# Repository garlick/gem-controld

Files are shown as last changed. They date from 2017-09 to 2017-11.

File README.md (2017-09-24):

### gem-controld

This project is a control system for a german equatorial telescope mount.
The mount is a Parallax series 125 head that has been retrofitted
with stepper motors on RA and DEC axes.

Electronics are based on the Beaglebone Black ARM-based single board
computer running Linux, a custom interface "cape" with two
[RS-422 transceivers](http://www.ti.com/product/sn65hvd379) which connect to
[Schneider Electric IM483i](http://motion.schneider-electric.com/downloads/manuals/im483i_ie.pdf) motion controllers, and GPIO based
[autogider](http://www.store.shoestringastronomy.com/guide_port_cables.pdf) and
[handbox](http://www.bbastrodesigns.com/handpad-assembly_notes.html) interfaces.
The electronics are packaged in a 7x7x5 DIN rail enclosure that mounts to
the telescope pier.

Software is based on reactive (event-driven) programming, with the goal
of keeping complexity down and separation of concerns among modules up.

### status

The handbox can be used to slew the telescope in two speeds, and the RA axis
tracks at a fixed sidereal rate.

The Meade LX200 and Tangent BBOX protocols can be used to sync the telescope
with a starmap program like Sky Safari, or control it (LX200 only).  A simple
pointing model is implemented with a one-star alignment available through
the remote application.

Autoguiding on an ST-4 interface works.

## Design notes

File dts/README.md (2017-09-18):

### device tree overlay

`GEM-IO` is the device tree overlay for the "cape" used in this project.
This description assumes Debian Jessie with kernel 4.x or similar.

We need the device tree compiler `dtc`:
```
sudo apt-get install device-tree-compiler
```

After installing compiled dtbo file into `/lib/firmware`, add
it to `/etc/default/capemgr`.
```
CAPE=GEM-IO
```

By default GEM-IO conflicts with  `BB-BONELT-HDMI`.  Disable it by following
instructions in `/boot/uEnv.txt`.  Currently it is to uncomment this
line:
```
##BeagleBone Black: HDMI (Audio/Video)/eMMC disabled:
#dtb=am335x-boneblack-overlay.dtb
```

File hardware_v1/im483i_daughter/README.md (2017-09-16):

### IM483i daughter board for GEM

This is a daughter board for the Intelligent Motion Systems, Inc
IM483i minature high performance microstepping module.  It breaks
out the RS-422 and hand controller inputs, and ties some outputs to
LED's mounted on the board.

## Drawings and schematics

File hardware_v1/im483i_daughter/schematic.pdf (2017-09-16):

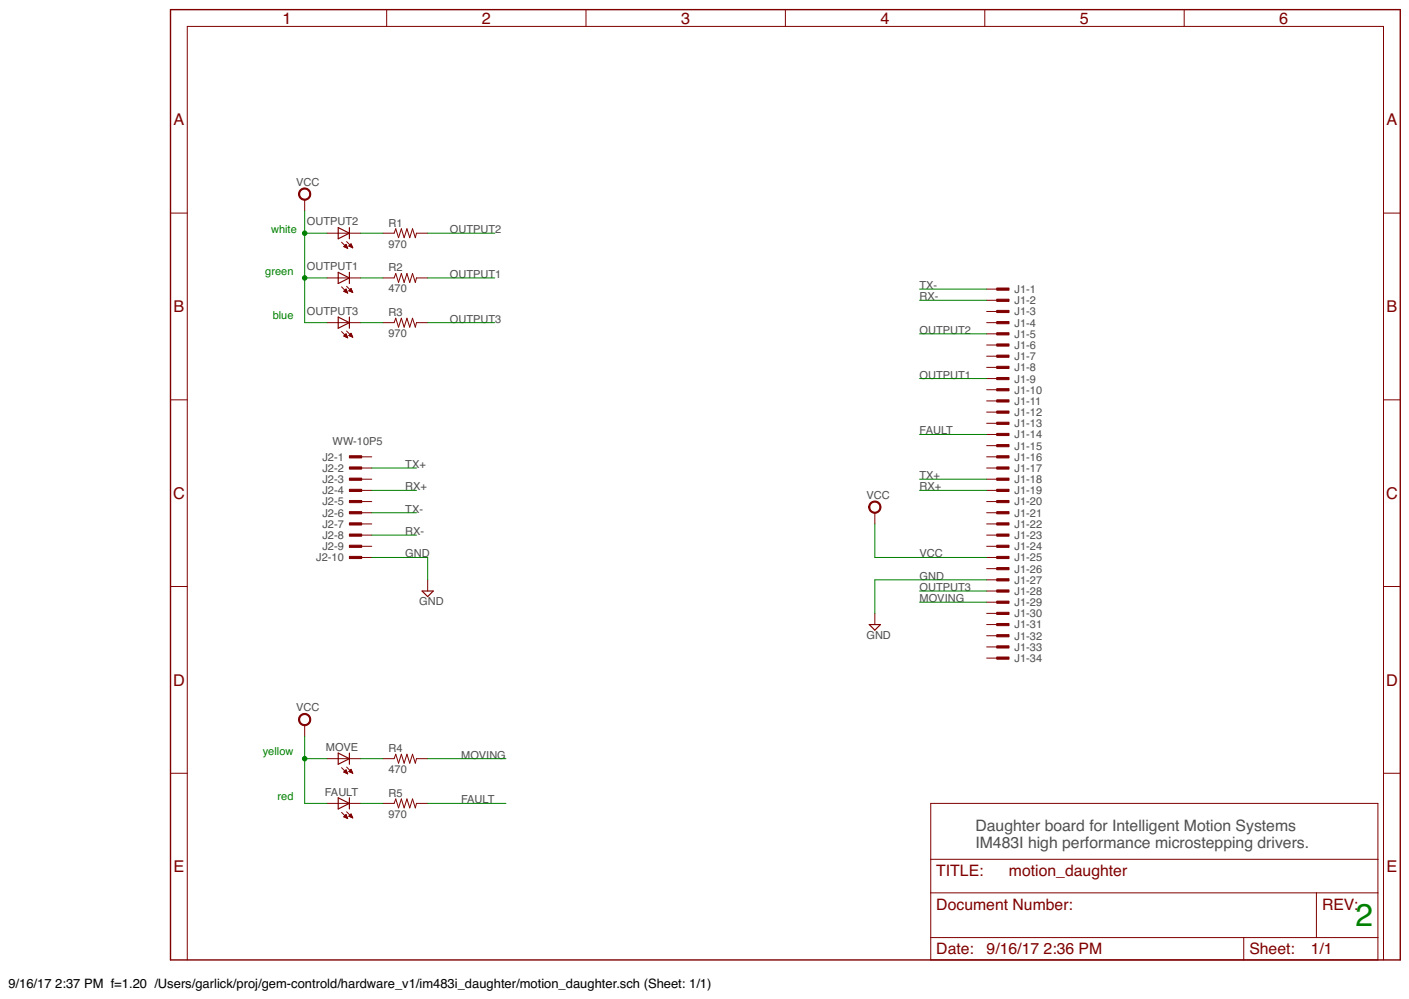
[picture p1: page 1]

Daughter board for Intelligent Motion Systems
IM483I high performance microstepping drivers.
TITLE:

Document Number: | REV: 2

Date: 9/16/17 2:36 PM | Sheet: 1/1

9/16/17 2:37 PM f=1.20 /Users/garlick/proj/gem-controld/hardware_v1/im483i_daughter/motion_daughter.sch (Sheet: 1/1)

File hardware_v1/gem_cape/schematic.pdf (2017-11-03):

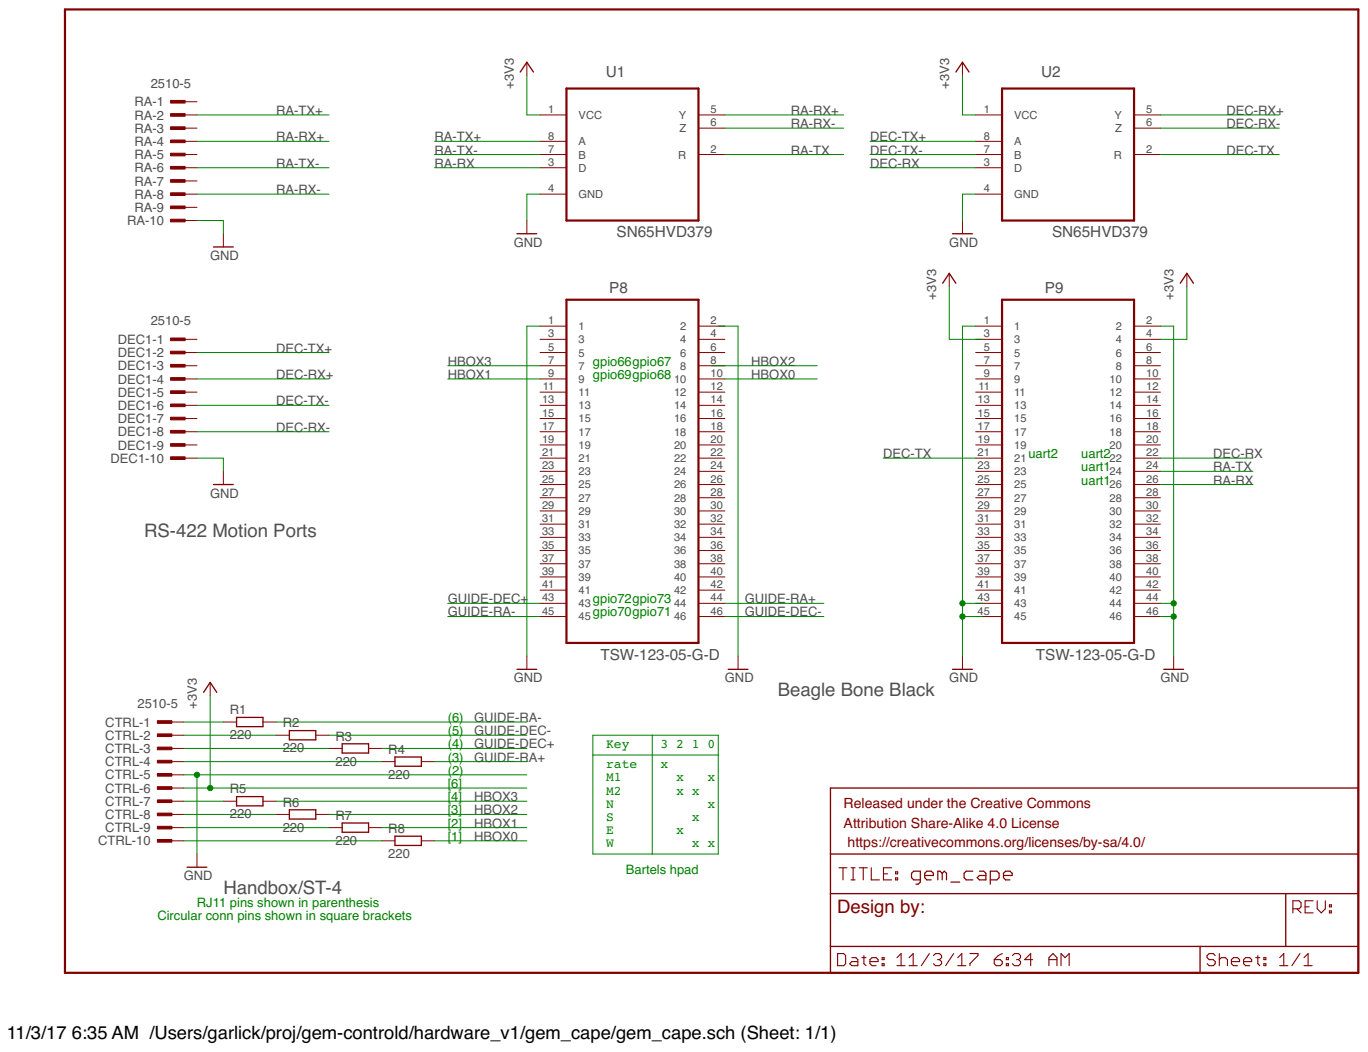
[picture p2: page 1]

DEC-RX- RA-TX

5 7 9 11 13 15 17 19 21 | 6 8 10 12 14 16 18 20 22

GUIDE-DEC+
GUIDE-RA-

GUIDE-DEC-

Key | 3 2 1 0
rate M1 M2 N S E | x x x x

Released under the Creative Commons Attribution Share-Alike 4.0 License

https://creativecommons.org/licenses/by-sa/4.0/

RJ11 pins shown in parenthesis Circular conn pins shown in square brackets

11/3/17 6:35 AM /Users/garlick/proj/gem-controld/hardware_v1/gem_cape/gem_cape.sch (Sheet: 1/1)

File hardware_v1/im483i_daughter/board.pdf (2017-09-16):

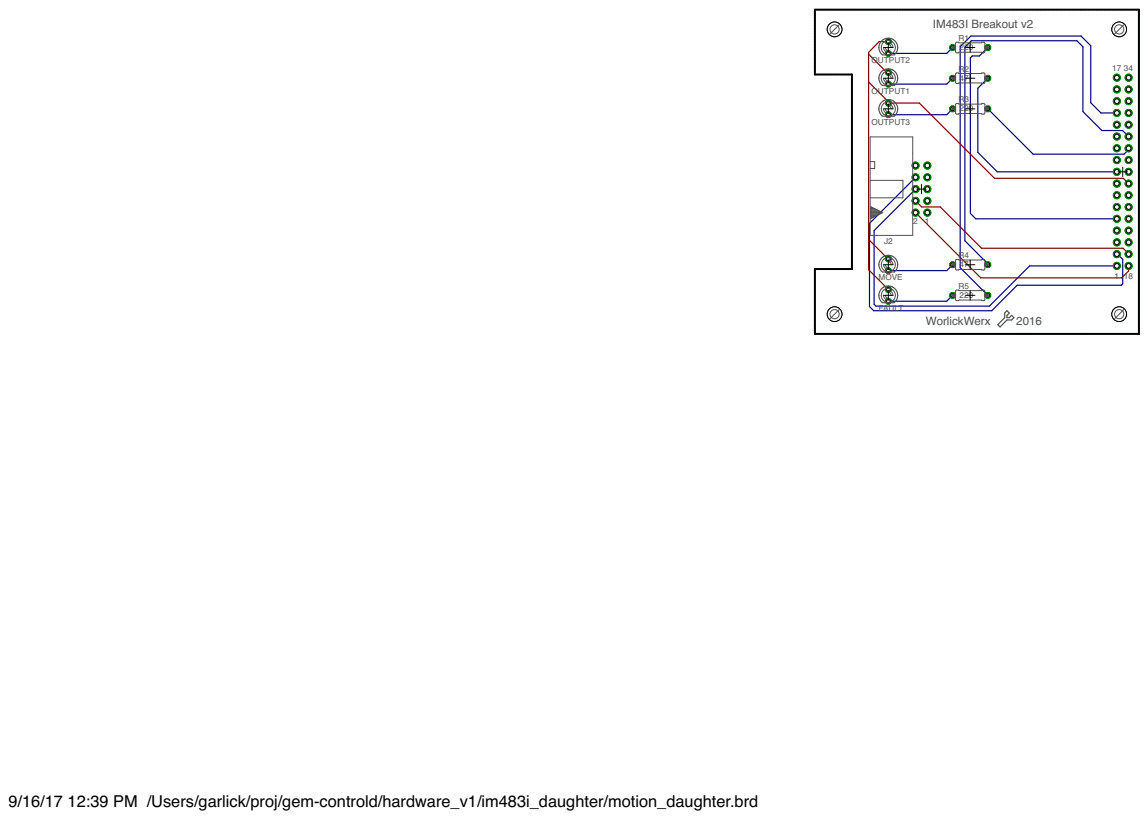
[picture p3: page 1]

9/16/17 12:39 PM /Users/garlick/proj/gem-controld/hardware_v1/im483i_daughter/motion_daughter.brd

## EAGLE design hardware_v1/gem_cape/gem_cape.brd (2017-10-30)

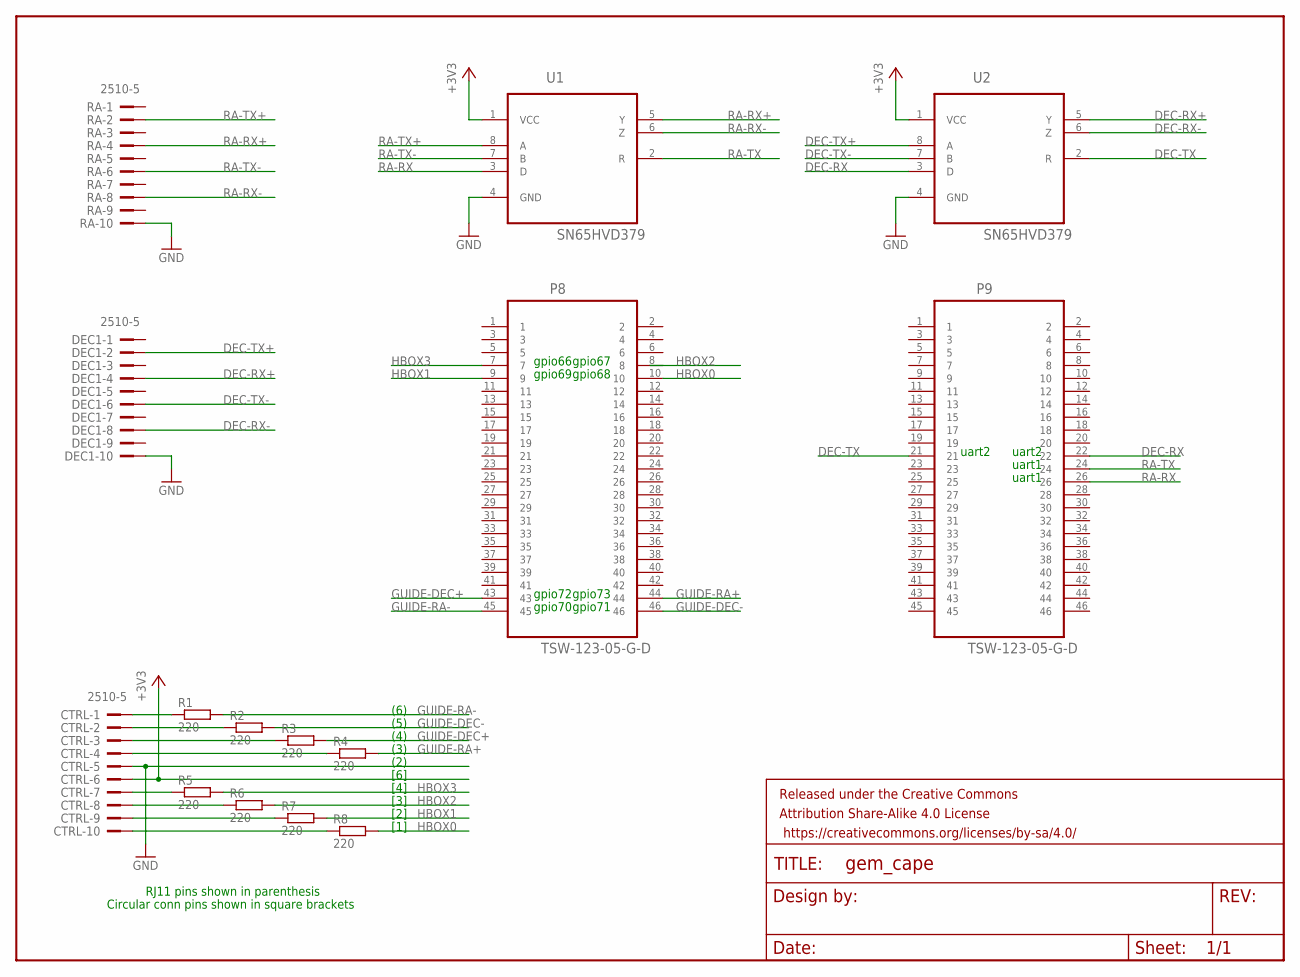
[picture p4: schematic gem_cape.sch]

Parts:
CTRL: 2510-5; PAK100/2500-5-10
DEC1: 2510-5; PAK100/2500-5-10
FRAME1: FRAME-LETTER; CREATIVE_COMMONS
P8, P9: TSW-123-05-G-D; SAMTEC_TSW-123-05-G-D
R1, R2, R3, R4, R5, R6, R7, R8: 220; R0805
RA: 2510-5; PAK100/2500-5-10
U1, U2: SN65HVD379; SOIC127P600X175-8N; MPN SN65HVD379

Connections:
+3V3: CTRL.6, U1.1 (VCC), U2.1 (VCC)
DEC-RX: P9.22, U2.3 (D)
DEC-RX+: DEC1.4, U2.5 (Y)
DEC-RX-: DEC1.8, U2.6 (Z)
DEC-TX: P9.21, U2.2 (R)
DEC-TX+: DEC1.2, U2.8 (A)
DEC-TX-: DEC1.6, U2.7 (B)
GND: CTRL.5, DEC1.10, RA.10, U1.4 (GND), U2.4 (GND)
GUIDE-DEC+: P8.43, R3.2
GUIDE-DEC-: P8.46, R2.2
GUIDE-RA+: P8.44, R4.2
GUIDE-RA-: P8.45, R1.2
HBOX0: P8.10, R8.2
HBOX1: P8.9, R7.2
HBOX2: P8.8, R6.2
HBOX3: P8.7, R5.2
unnamed: CTRL.1, R1.1
unnamed: CTRL.2, R2.1
unnamed: CTRL.3, R3.1
unnamed: CTRL.4, R4.1
unnamed: CTRL.7, R5.1
unnamed: CTRL.8, R6.1
unnamed: CTRL.9, R7.1
unnamed: CTRL.10, R8.1
RA-RX: P9.26, U1.3 (D)
RA-RX+: RA.4, U1.5 (Y)
RA-RX-: RA.8, U1.6 (Z)
RA-TX: P9.24, U1.2 (R)
RA-TX+: RA.2, U1.8 (A)
RA-TX-: RA.6, U1.7 (B)

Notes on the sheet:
(6)
(5)
(4)
(3)
(2)
[6]
[4]
[3]
[2]
[1]
RJ11 pins shown in parenthesis
Circular conn pins shown in square brackets
uart2
uart1
gpio68
gpio69
gpio67
gpio66
gpio72
gpio71
gpio73
gpio70

Board: 2 copper layers, 16 parts (2 on the bottom side), 30 nets, no tracks yet.

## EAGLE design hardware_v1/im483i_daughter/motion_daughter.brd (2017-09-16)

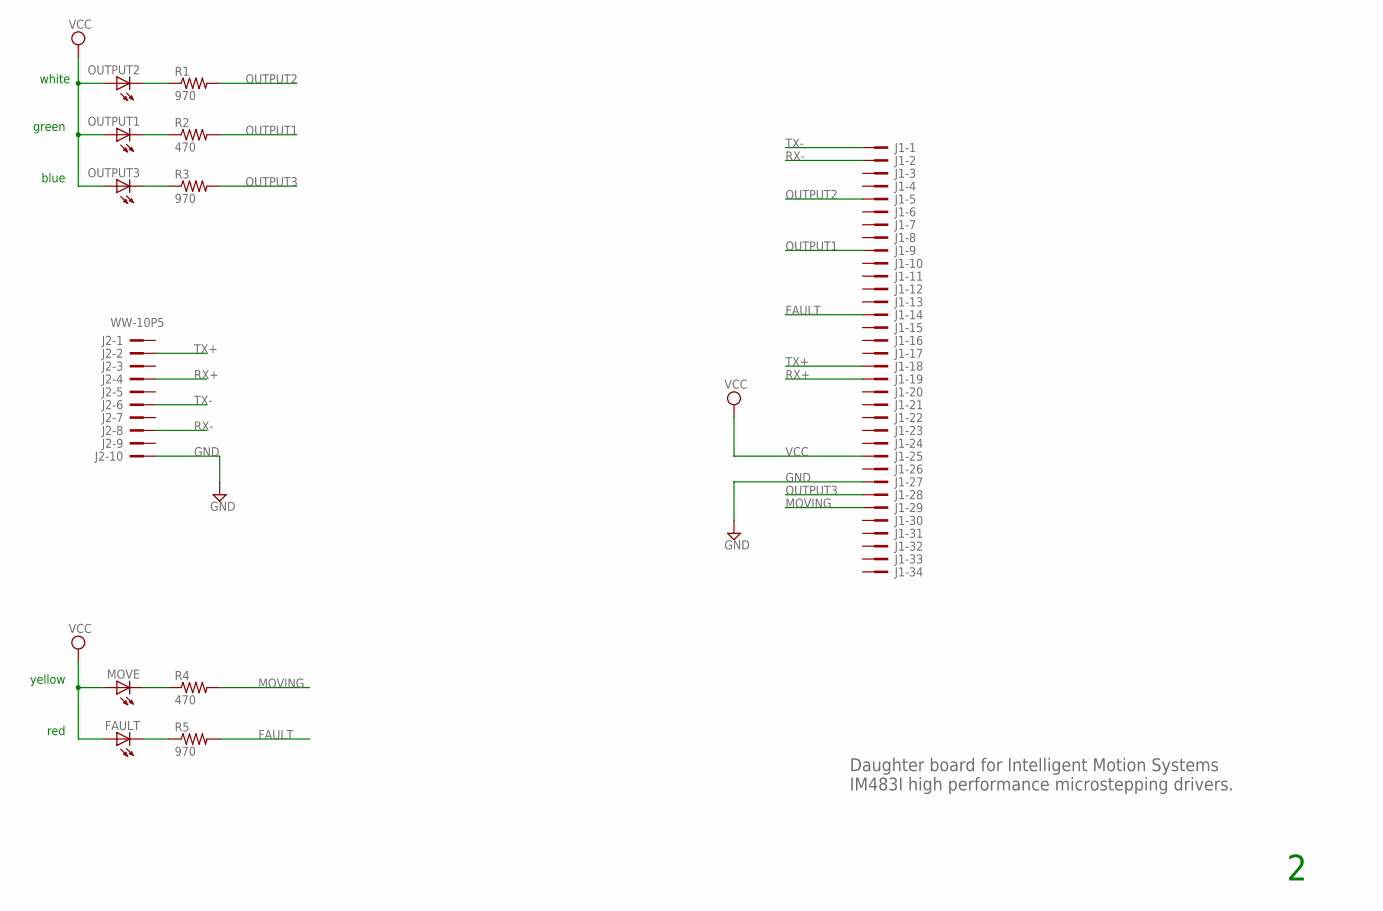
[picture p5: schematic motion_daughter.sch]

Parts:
FAULT: LED3MM
J1: WW-34P-SPECIALIM483I_HEADER; PAK100/2500-34
J2: WW-10P5; PAK100/2500-5-10
MOVE: LED3MM
OUTPUT1, OUTPUT2, OUTPUT3: LED3MM
R1, R3, R5: 970; 0207/7
R2, R4: 470; 0207/7

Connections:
FAULT: J1.P14, R5.2
GND: J1.P27, J2.10
MOVING: J1.P29, R4.2
unnamed: OUTPUT3.K (C), R3.1
unnamed: OUTPUT1.K (C), R2.1
unnamed: OUTPUT2.K (C), R1.1
unnamed: MOVE.K (C), R4.1
unnamed: FAULT.K (C), R5.1
OUTPUT1: J1.P9, R2.2
OUTPUT2: J1.P5, R1.2
OUTPUT3: J1.P28, R3.2
RX+: J1.P19, J2.4
RX-: J1.P2, J2.8
TX+: J1.P18, J2.2
TX-: J1.P1, J2.6
VCC: FAULT.A, J1.P25, MOVE.A, OUTPUT1.A, OUTPUT2.A, OUTPUT3.A

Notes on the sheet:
Daughter board for Intelligent Motion Systems IM483I high performance microstepping drivers.
white
green
blue
yellow
red

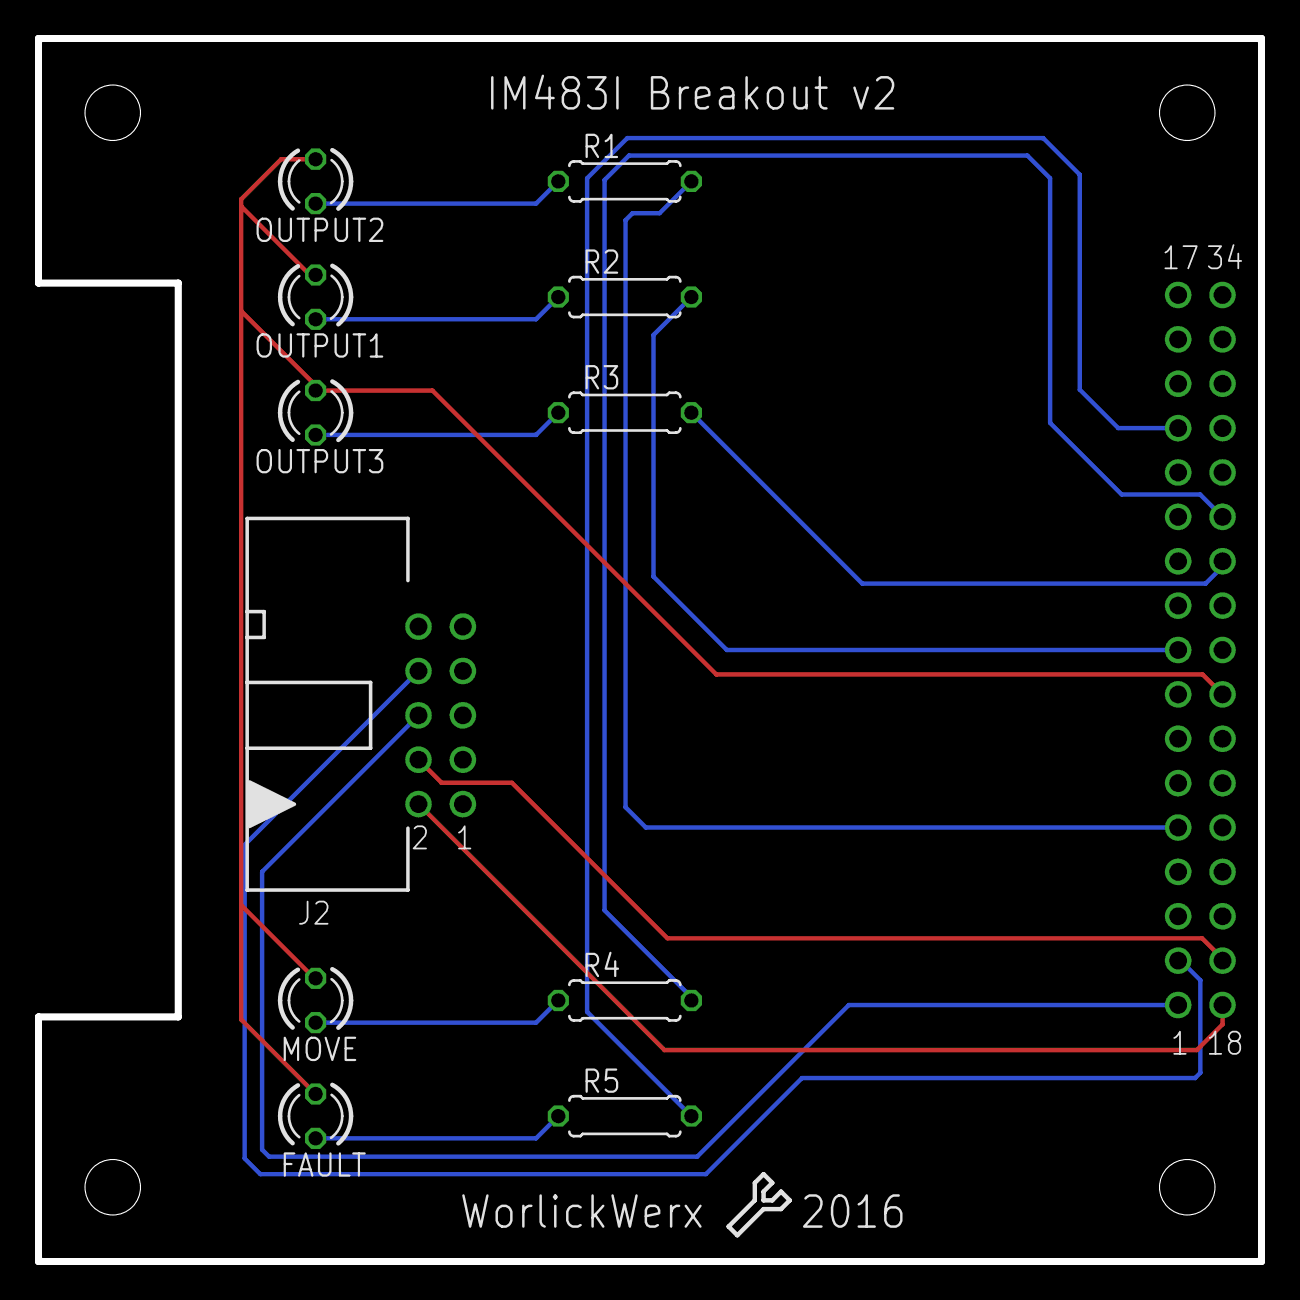
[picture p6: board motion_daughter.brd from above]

Board: 2 copper layers, 70.0 x 70.0 mm, 12 parts (0 on the bottom side), 16 nets.

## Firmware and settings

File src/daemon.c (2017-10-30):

/*****************************************************************************\
 *  Copyright (C) 2015 Jim Garlick
 *  Written by Jim Garlick <garlick.jim@gmail.com>
 *  All Rights Reserved.
 *
 *  This file is part of gem-controld
 *  For details, see <https://github.com/garlick/gem-controld>
 *
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
 *  You should have received a copy of the GNU General Public License along
 *  with this program; if not, write to the Free Software Foundation, Inc.,
 *  59 Temple Place, Suite 330, Boston, MA 02111-1307 USA.
 *  See also:  http://www.gnu.org/licenses/
\*****************************************************************************/

#include <stdio.h>
#include <stdlib.h>
#include <stdbool.h>
#include <unistd.h>
#include <libgen.h>
#include <getopt.h>
#include <errno.h>
#include <string.h>
#include <pwd.h>
#include <ev.h>
#include <math.h>
#include <assert.h>

#include "log.h"
#include "xzmalloc.h"
#include "gpio.h"
#include "configfile.h"
#include "motion.h"
#include "slew.h"
#include "hpad.h"
#include "guide.h"
#include "bbox.h"
#include "lx200.h"

char *prog = "";

struct prog_context {
    struct config opt;
    struct hpad *hpad;
    struct guide *guide;
    struct bbox *bbox;
    struct lx200 *lx200;
    struct motion *t;
    struct motion *d;
    struct ev_loop *loop;
    bool t_tracking;
    int slew;
    bool west;
};

struct motion *init_axis (struct config_axis *a, const char *name, int flags,
                          bool ccw);

void hpad_cb (struct hpad *h, void *arg);
void guide_cb (struct guide *g, void *arg);
void bbox_cb (struct bbox *bb, void *arg);
void motion_cb (struct motion *m, void *arg);
void lx200_pos_ha_cb (struct lx200 *lx, void *arg);
void lx200_pos_dec_cb (struct lx200 *lx, void *arg);
void lx200_slew_cb (struct lx200 *lx, void *arg);
void lx200_goto_cb (struct lx200 *lx, void *arg);
void lx200_stop_cb (struct lx200 *lx, void *arg);
void lx200_tracking_cb (struct lx200 *lx, void *arg);

int controller_velocity (struct config_axis *axis, double degrees_persec);

#define OPTIONS "+c:hMBLHGw"
static const struct option longopts[] = {
    {"config",               required_argument, 0, 'c'},
    {"help",                 no_argument,       0, 'h'},
    {"debug-motion",         no_argument,       0, 'M'},
    {"debug-bbox",           no_argument,       0, 'B'},
    {"debug-lx200",          no_argument,       0, 'L'},
    {"debug-hpad",           no_argument,       0, 'H'},
    {"debug-guide",          no_argument,       0, 'G'},
    {"west",                 no_argument,       0, 'w'},
    {0, 0, 0, 0},
};

static void usage (void)
{
    fprintf (stderr,
"Usage: gem [OPTIONS]\n"
"    -c,--config FILE    set path to config file\n"
"    -w,--west           observe west of meridian (scope east of pier)\n"
"    -M,--debug-motion   emit motion control commands and responses to stderr\n"
"    -B,--debug-bbox     emit bbox protocol to stderr\n"
"    -L,--debug-lx200    emit lx200 protocol to stderr\n"
"    -H,--debug-hpad     emit hpad events to stderr\n"
"    -G,--debug-guide    emit guide pulse events to stderr\n"
);
    exit (1);
}

int main (int argc, char *argv[])
{
    int ch;
    struct prog_context ctx;
    char *config_filename = NULL;
    int motion_flags = 0;
    int bbox_flags = 0;
    int hpad_flags = 0;
    int guide_flags = 0;
    int lx200_flags = 0;

    memset (&ctx, 0, sizeof (ctx));

    prog = basename (argv[0]);
    log_init (prog);

    while ((ch = getopt_long (argc, argv, OPTIONS, longopts, NULL)) != -1) {
        switch (ch) {
            case 'c':   /* --config FILE */
                config_filename = xstrdup (optarg);
                break;
            case 'M':   /* --debug-motion */
                motion_flags |= MOTION_DEBUG;
                break;
            case 'B':   /* --debug-bbox */
                bbox_flags |= BBOX_DEBUG;
                break;
            case 'L':   /* --debug-lx200 */
                lx200_flags |= LX200_DEBUG;
                break;
            case 'H':   /* --debug-hpad */
                hpad_flags |= HPAD_DEBUG;
                break;
            case 'G':   /* --debug-guide */
                guide_flags |= GUIDE_DEBUG;
                break;
            case 'w':   /* --west */
                ctx.west = true;
                lx200_flags |= LX200_POINT_WEST; // hint for unaligned starting
                break;
            case 'h':   /* --help */
            default:
                usage ();
        }
    }
    if (optind < argc)
        usage ();
    configfile_init (config_filename, &ctx.opt);
    if (!ctx.opt.hpad_gpio)
        msg_exit ("no hpad_gpio was configured");
    if (!ctx.opt.guide_gpio)
        msg_exit ("no guide_gpio was configured");

    if (!(ctx.loop = ev_loop_new (EVFLAG_AUTO)))
        err_exit ("ev_loop_new");

    ctx.t = init_axis (&ctx.opt.t, "t", motion_flags, true);
    motion_set_cb (ctx.t, motion_cb, &ctx);
    motion_start (ctx.loop, ctx.t);

    ctx.d = init_axis (&ctx.opt.d, "d", motion_flags, ctx.west ? true : false);
    motion_set_cb (ctx.d, motion_cb, &ctx);
    motion_start (ctx.loop, ctx.d);

    ctx.hpad = hpad_new ();
    if (hpad_init (ctx.hpad, ctx.opt.hpad_gpio, ctx.opt.hpad_debounce,
                   hpad_cb, &ctx, hpad_flags) < 0)
        err_exit ("hpad_init");
    hpad_start (ctx.loop, ctx.hpad);

    ctx.guide = guide_new ();
    if (guide_init (ctx.guide, ctx.opt.guide_gpio, ctx.opt.guide_debounce,
                   guide_cb, &ctx, guide_flags) < 0)
        err_exit ("guide_init");
    guide_start (ctx.loop, ctx.guide);

    ctx.bbox = bbox_new ();
    if (bbox_init (ctx.bbox, DEFAULT_BBOX_PORT, bbox_cb, &ctx, bbox_flags) < 0)
        err_exit ("bbox_init");
    bbox_set_resolution (ctx.bbox, ctx.opt.t.steps, ctx.opt.d.steps);
    bbox_start (ctx.loop, ctx.bbox);

    ctx.lx200 = lx200_new ();
    if (lx200_init (ctx.lx200, DEFAULT_LX200_PORT, lx200_flags) < 0)
        err_exit ("bbox_init");
    lx200_set_position_ha_cb (ctx.lx200, lx200_pos_ha_cb, &ctx);
    lx200_set_position_dec_cb (ctx.lx200, lx200_pos_dec_cb, &ctx);
    lx200_set_slew_cb (ctx.lx200, lx200_slew_cb, &ctx);
    lx200_set_goto_cb (ctx.lx200, lx200_goto_cb, &ctx);
    lx200_set_stop_cb (ctx.lx200, lx200_stop_cb, &ctx);
    lx200_set_tracking_cb (ctx.lx200, lx200_tracking_cb, &ctx);
    lx200_start (ctx.loop, ctx.lx200);

    ev_run (ctx.loop, 0);
    ev_loop_destroy (ctx.loop);

    bbox_stop (ctx.loop, ctx.bbox);
    bbox_destroy (ctx.bbox);

    lx200_stop (ctx.loop, ctx.lx200);
    lx200_destroy (ctx.lx200);

    guide_stop (ctx.loop, ctx.guide);
    guide_destroy (ctx.guide);

    hpad_stop (ctx.loop, ctx.hpad);
    hpad_destroy (ctx.hpad);

    motion_destroy (ctx.d);
    motion_destroy (ctx.t);

    return 0;
}

struct motion *init_axis (struct config_axis *a, const char *name, int flags,
                          bool ccw)
{
    struct motion_config cfg = {
        .resolution = a->resolution,
        .ihold      = a->ihold,
        .irun       = a->irun,
        .mode       = a->mode,
        .accel      = a->accel,
        .decel      = a->decel,
        .initv      = a->initv,
        .finalv     = a->finalv,
        .steps      = a->steps,
        .ccw        = ccw,
    };
    struct motion *m;

    if (!a->device)
        msg_exit ("%s: no serial device configured", name);
    if (!(m = motion_new (name)))
        err_exit ("%s: motion_create", name);
    if (motion_init (m, a->device, &cfg, flags) < 0)
        err_exit ("%s: motion_init %s", name, a->device);
    if (motion_set_io (m, MOTION_IO_OUTPUT1 | MOTION_IO_OUTPUT2
                                            | MOTION_IO_OUTPUT3) < 0)
        err_exit ("%s: motion set port", name);
    return m;
}

/* Given 'rate' enum from slew.h, look up configured rate in degrees/sec.
 * If 'neg' is true, make the velocity negative.
 * If 'track' is true, add the sidereal rate.
 */
double lookup_rate (struct config_axis *axis, int rate,
                    bool neg, bool track)
{
    double dps;

    switch (rate) {
        case SLEW_RATE_GUIDE:
            dps = axis->guide;
            break;
        case SLEW_RATE_SLOW:
            dps = axis->slow;
            break;
        case SLEW_RATE_MEDIUM:
            dps = axis->medium;
            break;
        case SLEW_RATE_FAST:
            dps = axis->fast;
            break;
        default:
            dps = 0.;
            break;
    }
    if (neg)
        dps *= -1.;
    if (track)
        dps += axis->sidereal;
    return dps;
}

/* A new slew "key press" event ignores a slew in progress on the
 * same axis and blindly sets the velocity.  The motion controllers can
 * handle this, even if direction is reversed.  The "key release" cancels
 * this and any other slew in progress.  The axes are independent.
 * It is possible to configure slew rates that will result in a controller
 * error;  motion_move_constant_dps() will return -1 with errno == EINVAL in
 * that case and the slew will fail.
 */
void slew_update (struct prog_context *ctx, int newmask, int rate)
{
    double dps;

    if ((newmask & SLEW_RA_PLUS) && (newmask & SLEW_RA_MINUS))
        newmask &= ~(SLEW_RA_PLUS + SLEW_RA_MINUS);
    if ((newmask & SLEW_DEC_PLUS) && (newmask & SLEW_DEC_MINUS))
        newmask &= ~(SLEW_DEC_PLUS + SLEW_DEC_MINUS);

    if ((newmask & SLEW_RA_PLUS) || (newmask & SLEW_RA_MINUS)) {
        dps = lookup_rate (&ctx->opt.t, rate, (newmask & SLEW_RA_MINUS),
                           ctx->t_tracking);
        if (motion_move_constant_dps (ctx->t, dps) < 0)
            err ("t: move at v=%.1lf*/s", dps);
    }
    else {
        if ((ctx->slew & SLEW_RA_PLUS) || (ctx->slew & SLEW_RA_MINUS)) {
            if (ctx->t_tracking) {
                dps = lookup_rate (&ctx->opt.t, 0, false, ctx->t_tracking);
                if (motion_move_constant_dps (ctx->t, dps) < 0)
                    err ("t: move at v=%.1lf*/s", dps);
            }
            else {
                if (motion_soft_stop (ctx->t) < 0) {
                    err ("t: stop");
                    if (motion_abort (ctx->t) < 0)
                        err ("t: abort");
                }
            }
        }
    }
    if ((newmask & SLEW_DEC_PLUS) || (newmask & SLEW_DEC_MINUS)) {
        dps = lookup_rate (&ctx->opt.d, rate, (newmask & SLEW_DEC_MINUS),
                           false);
        if (motion_move_constant_dps (ctx->d, dps) < 0)
            err ("d: move at v=%.1lf*/s", dps);
    }
    else {
        if ((ctx->slew & SLEW_DEC_PLUS) || (ctx->slew & SLEW_DEC_MINUS)) {
            if (motion_soft_stop (ctx->d) < 0) {
                err ("d: stop");
                if (motion_abort (ctx->d) < 0)
                    err ("d: abort");
            }
        }
    }
    ctx->slew = newmask;
}

/* After toggling t_tracking, or completion of a goto,
 * ensure that motion has (re-)enabled or disabled RA tracking
 * as appropraite.
 */
void update_tracking (struct prog_context *ctx)
{
    double dps;

    if (ctx->t_tracking) {
        dps = lookup_rate (&ctx->opt.t, SLEW_RATE_NONE, false, true);
        if (motion_move_constant_dps (ctx->t, dps) < 0)
            err ("t: move at v=%.1lf*/s", dps);
    }
    else {
         if (motion_soft_stop (ctx->t) < 0)
            err ("t: stop");
    }
}

void hpad_cb (struct hpad *h, void *arg)
{
    struct prog_context *ctx = arg;
    int dir = hpad_get_slew_direction (h);
    int rate = hpad_get_slew_rate (h);
    int ctrl = hpad_get_control (h);

    /* M1 - emergency stop
     */
    if ((ctrl & HPAD_CONTROL_M1)) {
        msg ("emergency stop");
        if (motion_abort (ctx->t) < 0) {
            err ("t: motion_abort");
            if (motion_abort (ctx->t) < 0) // one retry
                err ("t: motion_abort");
        }
        if (motion_abort (ctx->d) < 0) {
            err ("d: motion_abort");
            if (motion_abort (ctx->d) < 0) // one retry
                err ("t: motion_abort");
        }
        ctx->t_tracking = false;
        ctx->slew = 0;
        return;
    }
    /* M2 - toggle tracking
     */
    if ((ctrl & HPAD_CONTROL_M2)) {
        ctx->t_tracking = !ctx->t_tracking;
        update_tracking (ctx);
        return;
    }
    /* N,S,E,W
     */
    slew_update (ctx, dir, rate);
}

void guide_cb (struct guide *g, void *arg)
{
    struct prog_context *ctx = arg;
    int dir;

    if ((dir = guide_get_slew_direction (g)) < 0) {
        err ("guide_get_slew_direction");
        return;
    }
    slew_update (ctx, dir, SLEW_RATE_GUIDE);
}

/* LX200 protocol notifies us that slew "button" events
 * have occurred.
 */
void lx200_slew_cb (struct lx200 *lx, void *arg)
{
    struct prog_context *ctx = arg;
    int dir = lx200_get_slew_direction (lx);
    int rate = lx200_get_slew_rate (lx);

    slew_update (ctx, dir, rate);
}

/* Bbox protocol requests that we update "encoder" position.
 */
void bbox_cb (struct bbox *bb, void *arg)
{
    struct prog_context *ctx = arg;
    double t, d;

    if (motion_get_position (ctx->t, &t) < 0) {
        err ("%s: error reading t position", __FUNCTION__);
        return;
    }
    if (motion_get_position (ctx->d, &d) < 0) {
        err ("%s: error reading d position", __FUNCTION__);
        return;
    }
    bbox_set_position (bb, t, d);
}

/* LX200 protocol requests that we update position.
 */
void lx200_pos_ha_cb (struct lx200 *lx, void *arg)
{
    struct prog_context *ctx = arg;
    double t;
    double t_degrees;

    if (motion_get_position (ctx->t, &t) < 0) {
        err ("%s: error reading t position", __FUNCTION__);
        return;
    }
    t_degrees = 360.0 * (t / ctx->opt.t.steps);
    lx200_set_position_ha (lx, t_degrees);
}

void lx200_pos_dec_cb (struct lx200 *lx, void *arg)
{
    struct prog_context *ctx = arg;
    double d;
    double d_degrees;

    if (motion_get_position (ctx->d, &d) < 0) {
        err ("%s: error reading d position", __FUNCTION__);
        return;
    }
    d_degrees = 360.0 * (d / ctx->opt.d.steps);
    lx200_set_position_dec (lx, d_degrees);
}

/* LX200 protocol notifies us that we should retrieve goto target
 * coordinates and slew there.
 */
void lx200_goto_cb (struct lx200 *lx, void *arg)
{
    struct prog_context *ctx = arg;
    double t_degrees, d_degrees;
    double t, d;

    lx200_get_target (lx, &t_degrees, &d_degrees);

    msg ("goto %.1f*, %.1f*", t_degrees, d_degrees);

    if (t_degrees < -120 || t_degrees > 120
                         || d_degrees < -120 || d_degrees > 120) {
        msg ("goto out of range");
        return;
    }

    t = t_degrees/360.0 * ctx->opt.t.steps;
    d = d_degrees/360.0 * ctx->opt.d.steps;

    if (motion_goto_absolute (ctx->t, t) < 0)
        err ("t: set position");
    if (motion_goto_absolute (ctx->d, d) < 0)
        err ("d: set position");
}

/* LX200 protocol wants to stop all motion (abort a goto).
 * Tracking should continue.
 */
void lx200_stop_cb (struct lx200 *lx, void *arg)
{
    struct prog_context *ctx = arg;

    if (motion_soft_stop (ctx->t) < 0) {
        err ("t: soft stop");
        if (motion_abort (ctx->t) < 0)
            err ("t: abort");
    }
    if (motion_soft_stop (ctx->d) < 0) {
        err ("d: soft stop");
        if (motion_abort (ctx->d) < 0)
            err ("t: abort");
    }
    if (ctx->t_tracking)
        update_tracking (ctx);
}

/* LX200 protocol wants to know current RA tracking rate.
 */
void lx200_tracking_cb (struct lx200 *lx, void *arg)
{
    struct prog_context *ctx = arg;
    lx200_set_tracking_rate (lx, ctx->t_tracking ? ctx->opt.t.sidereal : 0);
}

/* Motion axis informs us that goto has completed.
 * Goto cancels the constant velocity motion of RA tracking,
 * so resume it here if enabled.
 * FIXME: need to account for lost tracking for the duration of the goto.
 */
void motion_cb (struct motion *m, void *arg)
{
    struct prog_context *ctx = arg;

    msg ("%s: goto end", motion_get_name (m));
    if (m == ctx->t && ctx->t_tracking)
        update_tracking (ctx);
}

/*
 * vi:tabstop=4 shiftwidth=4 expandtab
 */

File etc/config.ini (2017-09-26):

[t_axis]
device = /dev/ttyO1  ; serial device
mode = auto          ; resolution mode (auto, fixed)
resolution = 3       ; 1/8 velocity prescale for auto mode (0-8)
ihold = 1            ; hold current as pct of max (0-100)
irun = 5             ; run current as pct of max (0-100)
initv = 400          ; initial velocity for relative index (whole steps/sec)
finalv = 8031        ; final velocity for relative index (whole steps/sec)
accel = 5            ; ramp up slope (0-255)
decel = 5            ; ramp down slope (0-255)
steps = 403200       ; 1/360 worm * 15/42 belt drive * 1/400 steps
guide = 1E-2         ; guide velocity (degrees/sec)
slow = 1E-1          ; slow slew velocity (degrees/sec)
medium = 1           ; medium slew velocity (degrees/sec)
fast = 2.2           ; fast slew velocity (degrees/sec)
sidereal = 4.17075E-3; sidereal tracking rate (degrees/sec)

[d_axis]
device = /dev/ttyO2
resolution = 3
mode = auto
ihold = 1
irun = 5
initv = 400
finalv = 8031
accel = 10
decel = 10
steps = 201600       ; steps/rev: 1/180 worm * 15/42 belt drive * 1/400 steps
guide = 1E-2
slow = 1E-1
medium = 2
fast = 3.5

[hpad]
gpio = 68,69,67,66   ; bartels handpad gpio pins (bits 0,1,2,3)
debounce = .010      ; debounce (sec)

[guide]
gpio = 72,71,73,70   ; guide port gpio pins (bits DEC+,DEC-,RA+,RA-)
debounce = .010      ; debounce (sec)

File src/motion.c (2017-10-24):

/*****************************************************************************\
 *  Copyright (C) 2015 Jim Garlick
 *  Written by Jim Garlick <garlick.jim@gmail.com>
 *  All Rights Reserved.
 *
 *  This file is part of gem-controld
 *  For details, see <https://github.com/garlick/gem-controld>
 *
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
 *  You should have received a copy of the GNU General Public License along
 *  with this program; if not, write to the Free Software Foundation, Inc.,
 *  59 Temple Place, Suite 330, Boston, MA 02111-1307 USA.
 *  See also:  http://www.gnu.org/licenses/
\*****************************************************************************/

/* motion.c - communicate with IMS im483i indexer */

/* N.B. The im483i can only handle one command a time.  It is "busy" if a
 * command has been sent, but a result has not yet been received.
 *
 * Commands are terminated with \r.
 * Results are terminated with \r\n.
 *
 * Communication is assumed to be in single mode, not party line.
 *
 * The im483ie (encoder version) should work but no support for encoder
 * based operations is included.
 *
 * The Z1 mode, which causes position updates terminated with \r to be sent
 * continuously until the next command, is not used here, and is not handled
 * by the command/result framing code.
 *
 * Ref: High Performance Microstepper Driver & Indexer Software Reference
 * Manual, Intelligent Motion Systems, Inc.
 * https://motion.schneider-electric.com/downloads/manuals/imx_software.pdf
 * http://lennon.astro.northwestern.edu/Computers/IMSmanual.html
 */

#include <fcntl.h>
#include <unistd.h>
#include <stdlib.h>
#include <termios.h>
#include <errno.h>
#include <stddef.h>
#include <stdint.h>
#include <stdbool.h>
#include <string.h>
#include <stdio.h>
#include <assert.h>
#include <stdarg.h>
#include <math.h>
#include <ev.h>

#include "log.h"
#include "motion.h"

#define MAX_CMD     80
#define MAX_BUF     1024

enum {
    SEND_EXPECT_ECHO = 1,
};

struct motion {
    int fd;
    char *name;
    int flags;
    ev_io io_w;
    ev_timer status_poll_w;
    ev_timer timeout_w;
    bool timeout;
    struct ev_loop *main_loop;
    struct ev_loop *tmp_loop;
    char inbuf[MAX_BUF];
    int inbuf_len;
    bool busy;
    motion_cb_f cb;
    void *cb_arg;
    struct motion_config cfg;
};

static const double status_poll_sec = 0.3;  // poll period during goto

static const double timeout_sec = 10.;  // waiting for result - give up
static const double warn_sec = 4.;      // waiting for result - warn

static int result_recv (struct motion *m, char *buf, int len);
static void result_clear (struct motion *m);
static int serial_send (int fd, const char *s);


/* Translate unprintable characters into readable debug output.
 * Caller must free resulting string.
 */
static char *toliteral (const char *s)
{
    int len = strlen (s) * 4 + 1;
    char *buf;
    const char *p = s;

    if ((buf = malloc (len))) {
        memset (buf, 0, len);
        while (*p) {
            if (*p == '\r')
                sprintf (buf + strlen (buf), "\\r");
            else if (*p == '\n')
                sprintf (buf + strlen (buf), "\\n");
            else if (*p < ' ' || *p > '~')
                sprintf (buf + strlen (buf), "\\%.3o", *p);
            else
                buf[strlen (buf)] = *p;
            p++;
        }
    }
    return buf;
}

/* If busy, wait for result, then clear result buffer.
 * Send string to serial port with \r terminator, then set busy flag.
 */
static int command_send (struct motion *m, int flags, const char *s)
{
    char buf[MAX_CMD];

    if (m->busy) {
        if (result_recv (m, NULL, 0) < 0)
            return -1;
    }
    result_clear (m);

    if (snprintf (buf, sizeof (buf), "%s\r", s) >= sizeof (buf)) {
        errno = EINVAL;
        return -1;
    }
    if (m->flags & MOTION_DEBUG) {
        char *cpy = toliteral (buf);
        fprintf (stderr, "%s>'%s'\n", m->name, cpy);
        free (cpy);
    }
    if (serial_send (m->fd, buf) < 0)
        return -1;

    m->busy = true;

    if ((flags & SEND_EXPECT_ECHO)) {
        char result[MAX_CMD];
        if (result_recv (m, result, sizeof (result)) < 0)
            return -1;
        if (strncmp (buf, result, strlen (result)) != 0) { // ignore \r in buf
            errno = EPROTO;
            return -1;
        }
    }

    return 0;
}

/* printf-style wrapper for command_send().
 */
static int command_sendf (struct motion *m, bool flags, const char *fmt, ...)
{
    va_list ap;
    char *s = NULL;
    int rc;

    va_start (ap, fmt);
    rc = vasprintf (&s, fmt, ap);
    va_end (ap);
    if (rc < 0)
        goto done;
    rc = command_send (m, flags, s);
done:
    free (s);
    return rc;
}

/* helper for result_clear() and result_recv() */
static int result_consume (struct motion *m, char *buf, int len)
{
    char *p;
    int used;

    if (!(p = strstr (m->inbuf, "\r\n")))
        return -1;
    *p = '\0';

    if ((m->flags & MOTION_DEBUG)) {
        char *cpy = toliteral (m->inbuf);
        fprintf (stderr, "%s<'%s\\r\\n'\n", m->name, cpy);
        free (cpy);
    }

    if (buf)
        snprintf (buf, len, "%s", m->inbuf);

    used = strlen (m->inbuf) + 2;
    memmove (m->inbuf, m->inbuf + used, m->inbuf_len - used);
    m->inbuf_len -= used;
    m->inbuf[m->inbuf_len] = '\0';
    m->busy = false;
    return 0;
}

/* Clear the result buffer.
 */
static void result_clear (struct motion *m)
{
    while (result_consume (m, NULL, 0) == 0)
        ;
}

static void timeout_cb (struct ev_loop *loop, ev_timer *w, int revents)
{
    struct motion *m = (struct motion *)((char *)w
                        - offsetof (struct motion, timeout_w));

    ev_break (loop, EVBREAK_ALL);
    m->timeout = true;
}
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

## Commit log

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2015-02-22 gpio: assign buttons to motion controls
    N, S, E, W set configurable slew velocities (fast/slow setting).
    M1+M2 exits the program, termination all motion.
    M1 displays position (X,Y)
2015-02-24 make microstep resolution configurable
    Disable M1+M2 quit - not a useful feature and bad
    to hit accidentally.
    Empirically determine the RA tracking number.
    It sees we need more resolution to further fine tune.
    Make microstep resolution configurable. Does not appear
    to change velocity units which are "equivalent full steps/sec"?
    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
2015-03-01 Add more config params
    Add the following IM483I params
    - hold/run current
    - accel/decel ramp slope
    - track for dec (why I'm not sure)
    and factor the config parsing code to avoid duplication.
    [config.ini, motion.c]
2015-03-01 gpio: rework for more general use with event loop
    [gpio.c]
2015-03-01 gem: rework handpad interface with ev_loop
    [config.ini, gpio.c]
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2015-03-22 libutil: add ev_zmq libev zeromq watcher
    Pull in this custom aggregrate watcher from the flux-core project.
    This allows zeromq sockets to be integrated with the libev event loop.
2015-03-23 enable zeromq ROUTER socket for handling requests
    Bind to a configured ROUTER socket URI, then create a libev watcher
    to respond when a message arrives.
    Disable czmq's default signal handling, which caused systemd to get
    stuck when it tries to stop/restart gem-contrld.
    [config.ini]
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2015-03-23 daemon: add --soft-init to avoid zeroing position
    [motion.c]
2015-03-23 add goto command, disable motion timeouts
    A goto command gets a response from the motion controller immediately.
    However, the next goto or track command will not be responded to
    until the first goto finishes. Thus (a) timeouts are inappropriate, and
    (b) with no timeouts, issuing the second command blocks the event loop,
    so it should be avoided if possible, e.g. by polling the position.
    [motion.c]
2015-03-23 config: reflect actual telescope gear ratios
    For parallax 125: DEC axis has double the gear ratio of RA.
    Cut DEC slew/adjust velocities in half to match RA.
    Double RA acceleration to match DEc.
    Set the number of steps per revolution 'steps' for each axis.
2015-03-24 don't allow motion until mount has been zeroed
    The handpad now has 'zero' and 'start/stop tracking' assigned
    to the two mode buttons. Allow handpad slewing but disable
    remote goto, park, or read position until the mount has been
    zeroed. It can be zeroed at the handpad or remotely.
    Also don't start initial tracking until requested (remotely or
    via the handpad). This is not because it is a danger so much
    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
2015-03-24 daemon: fix logic error in handpad callback
    Before the mount has been zeroed, RA tracking should not begin
    after the first handpad adjustment. The zero button has to be
    pressed (or the remote equivalent).
    [daemon.c]
2015-03-24 Use arcsec/sec for tracking units
    Tracking op now accepts velocities in arcsec/sec and we calculate the
    appropriate controller velocity based on configured steps/rev, mode,
    and resolution.
    Remove the 'track' configuration, and instead calculate the sidereal
    tracking rate based on the above and a constant sidereal arcsec/sec.
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2015-03-24 drop STEPS op as we are scaling on server side
    No need for a remote client to query this value as all interactions
    over the wire will be in standard units.
2015-03-24 Use arcsec for positioning
    Over the wire use tenth-arcsec for GOTO and POSITION.
    Convert to controller positions at the server.
    Also switch from arcsec/sec to tenth-arcsec/sec over the wire for TRACK.
2015-03-24 modify STOP to abort slew in progress
    The STOP op used to set velocities to zero, but these requests
    get queued up on the motion controller behind any in progress
    goto commands, so they cannot abort a goto gone wrong.
    Instead send '@' which aborts everything (decelerating nicely).
    [daemon.c, motion.c]
2015-03-25 motion: tolerate a soft start w/o losing origin
    Avoid doing a ^C reset in motion_init(), unless MOTION_RESET
    flag is present, as this resets the origin. Modify the
    motion_init() "initiate communications" sequence to be idempotent.
    Add motion_set_port(), motion_get_port() for general purpose GPIO
    access, and stop touching the green LED in motion_init().
    At startup, read the green LED state, and if set (off) for both
    controllers, initialize 'zeroed' state to true. When 'zeroed'
    state is changed from false to true, set the green LED state.
    Thus we can tolerate a linux/gem-controld restart without having
    to reset the origin.
    Drop the --soft-start option.
    [daemon.c, motion.c]
2015-03-25 motion: rename motion_abort() to motion_stop()
    This distinguishes it from the nastier ESC abort
    which immediately halts motion without deceleration.
2015-03-25 don't stop motion when warm starting gem-controld
    motion_init() should not send a soft stop command. Add a 'coldstart'
    parameter to motion_init() so it can tell inform the caller whether
    the hello sequence detected an already running controller.
    Avoid initializing resolution, mode, current, etc. if coldstart returns
    false. At least one of these commands has the effect of stopping motion.
    Finally, initialize 'stopped' based on the actual motion status of
    the controller so handpad M2 stop toggle works as expected.
    [daemon.c, motion.c]
2015-03-25 use hundredth-arcsec units on the wire
    This change simply avoids discarding resolution via the protocol
    that the motion controllers will accept.
    [daemon.c]
2015-03-25 standardize variable names, define origin
    To be clear that motiond only handles raw telescope position,
    not anything to do with the sky, name position coordinates
    to (t,d), in arcseconds.
    Motion controller cooordinates are named (x,y), in full steps.
    Define the origin to be motion (0,0) and position (0,90*60*60),
    the latter to roughly align with (LHA,DEC), e.g. pointing at
    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
2015-03-25 account for t_axis direction reversal
    Set 'steps' negative for t_axis, then make sidereal constant positive.
    This way (t,d) has the same sign as (LHA,DEC).
    [config.ini, daemon.c]
2015-03-26 add configurable limits to avoid unsafe positions
    Add a 'low_limit' and 'high_limit' configuration in arcsecs for
    the two axes. The server returns EINVAL if the user tries to GOTO
    an illegal position. Similarly, if the user configured illegal
    park values, return EINVAL to the PARK command.
    [config.ini, configfile.c, daemon.c]
2015-03-26 return EAGAIN to GOTO/PARK when motion in progress
    Query the motion controllers to ensure they are not already
    carrying out a move before allowing a GOTO or PARK move to
    be queued, since this would stall the event loop.
    [daemon.c]
2015-03-27 regularly publish position information
    Add a new zeromq pub/sub socket. Add a timer to motiond, and
    when it fires, publish the telescope position. When idle/tracking
    do this every 5s, but increase frequency when a move is in progress.
    Modify 'gem plot' so that it subscribes to these updates and
    passively waits for position updates, pushing them to the gnplot window
    at whatever frequency they are offered.
2015-03-27 add motiond --force option
    If started with the --force option, motiond performs a factory
    reset on the motion controllers, which can get them out of a
    bad state, but resets the origin.
    The loss of origin is handled properly, e.g. motion commands
    return EINVAL until the mount is re-zeroed.
    [daemon.c]
2015-07-02 add 'f' axis
    Add axis to config data structure so we can have an [f_axis] stanza
    in the config file.
    - define 'steps' to be steps per meter of focus travel
    (compare steps/rev for t, d axes)
    - define low_limit, high_limit to be in microns
    (compare arcsec to t, d axes)
    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
2015-07-02 motiond: add FLAG_F_TRACKING
    When handpad is controlling focus, motion controller may be in
    constant velocity state, as opposed to executing a move
    (FLAG_F_MOVING).
2015-07-03 implement usable focus commands
    Change the meaning of OP_FOCUS to a relative distance to move the
    focus in our out. We use motion_set_index() for that.
    Add initv/finalv config options and corresponding motion commands,
    motion_set_initial_velocity() and motion_set_final_velocity()
    so that start/end slew speeds for relative index can be configured.
    Implement this in gem-motiond initialization.
    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
2017-09-16 hardware_v1: add motion daughter board files
    Custom library parts consist of 36p and 10p 3m 100 mil
    headers orig from (eagle libs? element13?) libs,
    with hole sizes adjusted up slightly to match bits on hand,
    pin numbering of 36p adjusted for odd IMS layout, and
    silk adjusted for new pin numbers and drop artwork for
    connector shroud.
    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
    [motion_daughter.brd, motion_daughter.sch]
2017-09-16 hardware_v1: change resistor values, add pdfs
    [motion_daughter.brd, motion_daughter.sch]
2017-09-17 src/daemon: avoid useless typedef for prog_context
    [daemon.c]
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2017-09-19 bbox: [cleanup] fix whitespace and line length
    [bbox.c]
2017-09-19 daemon: add --west option
    The RA motor runs with a positive tracking velocity when
    the telescope is on the east side of the pier, observing
    west of the meridian. It runs with a negative velocity
    when tracking with the telescope on the west side of the
    pier, observing east of the meridian.
    Make the default be "observing east", and add a --west
    option to reverse the polarity of the RA axis for
    "merdian flip".
    Drop the sign from the 'steps' attribute on the t axis
    config file.
    [config.ini, daemon.c]
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2017-09-19 bbox: scale "encoder resolution" to 16K
    Limit "encoder resolution" to 16K and scale positions
    accordingly if the resolution exceeds that.
    This is just in case returning more than 5 digits of
    precision is a problem for some clients, or in case
    a 16-bit short is being used to store values.
    The decreased resolution won't matter much for syncing
    the position of the telescope with a star map, which
    is the primary goal of the bbox interface.
    [bbox.c]
2017-09-19 daemon: correct RA polarity
    [daemon.c]
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2017-09-22 daemon: fix --debug-lx200
    Due to a typo, the bbox flags were being set
    when --debug-lx200 was requested.
    [daemon.c]
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2017-09-24 drop two stage option parsing in commands
    The command line doesn't override any config file
    entries anymore, so drop the two stage option parsing
    from the daemon and test programs.
    [daemon.c, test-hpad.c]
2017-09-24 daemon: map hpad M1 key to emergency stop
    Problem: need a way to manually stop the telescope if
    things go wrong.
    Pressing M1 executes a "soft stop" (with deceleration) on
    both axes.
    [daemon.c]
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2017-09-24 lx200: add slew rate commands
    Support the commands for setting the slew rate to
    one of four fixed values. Add an accessor so that
    the slew command callback can get the current rate.
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2017-09-30 hpad: fix control button handling
    Problem: M1, M2 hpad decoding doesn't work.
    A few days ago I broke this when restructuring the code.
    Add missing breaks to switch statement.
    Also re-add debugging output for control keys and
    velocity switch.
    [hpad.c]
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2017-09-30 motion: switch to reactive model
    Switch to reactive programming model internally.
    Drop code to detect whether motion controllers
    have been previously initialized, and instead
    unconditionally perform a software reset and
    load configuration parameters. RA tracking is
    always disabled on startup.
    Open serial port in non-blocking mode and perform
    all reads through an event loop io watcher.
    If a response needs to be read synchronously,
    do it, with timeout, in a temporary reactor that
    only has the io watcher and timer active.
    Implement a reactor based poller to monitor
    motion status during a goto, and add a callback
    to the daemon, so it can re-enable tracking
    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
    [daemon.c, motion.c]
2017-10-07 daemon: motion_abort() if motion_soft_stop() fails
    Since im483i commands occasionally time out, and a failed
    motion_soft_stop(), such as upon release of a slew button,
    can leave the telescope in motion, issue a motion_abort()
    if motion_soft_stop() fails.
    [daemon.c]
2017-10-07 motion: hide axis velocity calculation
    Add 'ccw' (step direction reversal) and 'steps' (number
    of steps per revolution) to the motion configuration, and
    then allow slew/tracking velocity to be set in degrees per
    second, thus hiding some im483i specific code in the motion
    module where it belongs.
    [daemon.c, motion.c]
2017-10-07 daemon: if --west, flip DEC not RA (!)
    Of course after a meridian flip, it is the DEC axis that must
    be reversed, not RA. The RA axis is not reoriented so it still
    must track the earth's rotation in the same direction! Duh.
    [daemon.c]
2017-10-07 daemon: refuse goto if not within +/-90*
    It's probably safe to presume that the telescope is zeroed
    within 90* of its furthest reach on either axis. Therefore,
    refuse a goto that is outside of that range.
    Running down a bug in the pointing code that occasionally
    tries to take one axis on a very long trip the wrong way round.
    This defensive posture will be OK even after the bug is found.
    [daemon.c]
2017-10-07 daemon: reverse RA tracking direction
    In the last PR, I manage to set RA tracking the wrong
    direction. Reverse.
    [daemon.c]
2017-10-07 motion: motion_abort() should wait for response
    If the emergency stop fails we want to capture that, so
    block until the response is received.
    If user presses M1 key, log "emergency stop".
    [daemon.c, motion.c]
2017-10-07 motion: make simple commands synchronous
    Tighten up the im483i protocol parsing a bit by forcing
    simple commands to wait for an echo response indicating they
    have been processed. This ensures any unexpected response or
    timeout is associated wtih the offending command in error messages.
    Not much was probably gained by the "fire and forget" approach
    being used, where the next command has to wait if the previous
    one is still being handled. Since there is so much polling for
    position in the lx200 implementation, there is much blocking anyway.
    [motion.c]
2017-10-07 lx200: fix typo in set target object handler
    Problem: When lx200 protocol asks to update target RA,
    if using high precision, dec is updated instead.
    Fix typo - update ra in that case.
2017-10-07 lx200, point: split set_position() into ha, dec
    Problem: For every SkySafari/LX200 request for position,
    the motion controllers receive two requests.
    lx200 protocol splits position request into separate
    RA and DEC requests. Since our motion, point, and lx200 callbacks
    are not split, this requires each single-axis fetch to do the
    work for both axes.
    Split these functions and callbacks into one for each axis.
    [daemon.c]
2017-10-07 daemon: allow +-120&* of motion instead of +-90*
    Problem: if mount is powered up (zeroed) pointing at polaris,
    the dec axis may need to slew beyond 90 degrees to cover one half
    the visible sky.
    Change the limit to +-120*.
    [daemon.c]
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2017-10-30 hardware_v1/gem_cape: import WIP
    [gem_cape.brd, gem_cape.sch]
2017-11-02 hardware_v1/gem_cape: add hpad truth to schematic
    [gem_cape.sch]
2017-11-03 hardware_v1/gem_cape: add power pins
    [gem_cape.sch]

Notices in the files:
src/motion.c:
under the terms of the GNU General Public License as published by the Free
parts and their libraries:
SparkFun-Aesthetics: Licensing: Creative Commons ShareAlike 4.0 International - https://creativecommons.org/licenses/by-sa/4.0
